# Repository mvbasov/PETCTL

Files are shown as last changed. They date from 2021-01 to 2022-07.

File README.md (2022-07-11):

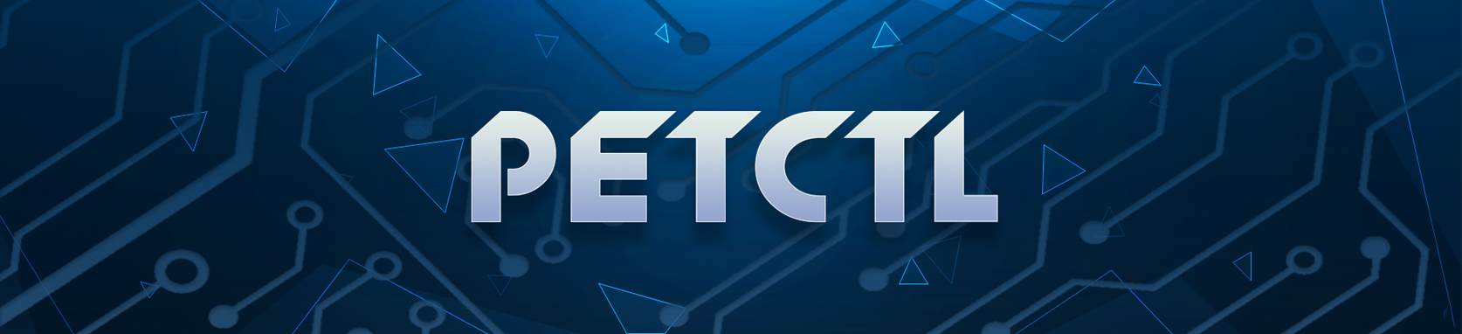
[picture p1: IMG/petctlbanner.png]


# PETCTL

Это контролер управляющий станком преобразующим ленту нарезанную из PET бутылок в волокно пригодное для 3D печати.

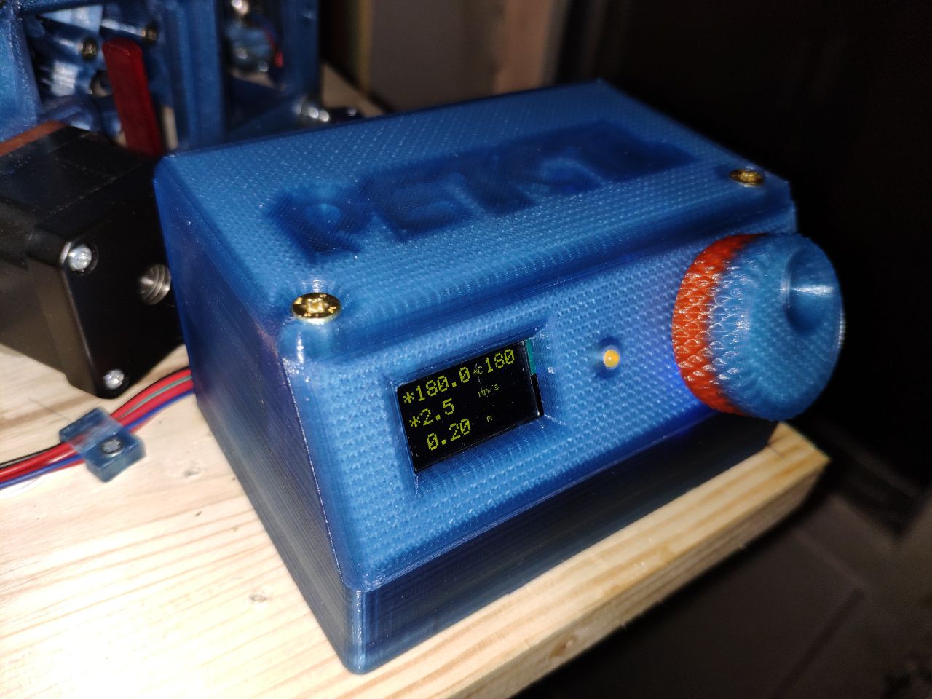
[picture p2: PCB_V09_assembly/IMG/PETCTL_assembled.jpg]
PETCTL assembled


Вот схема:

---

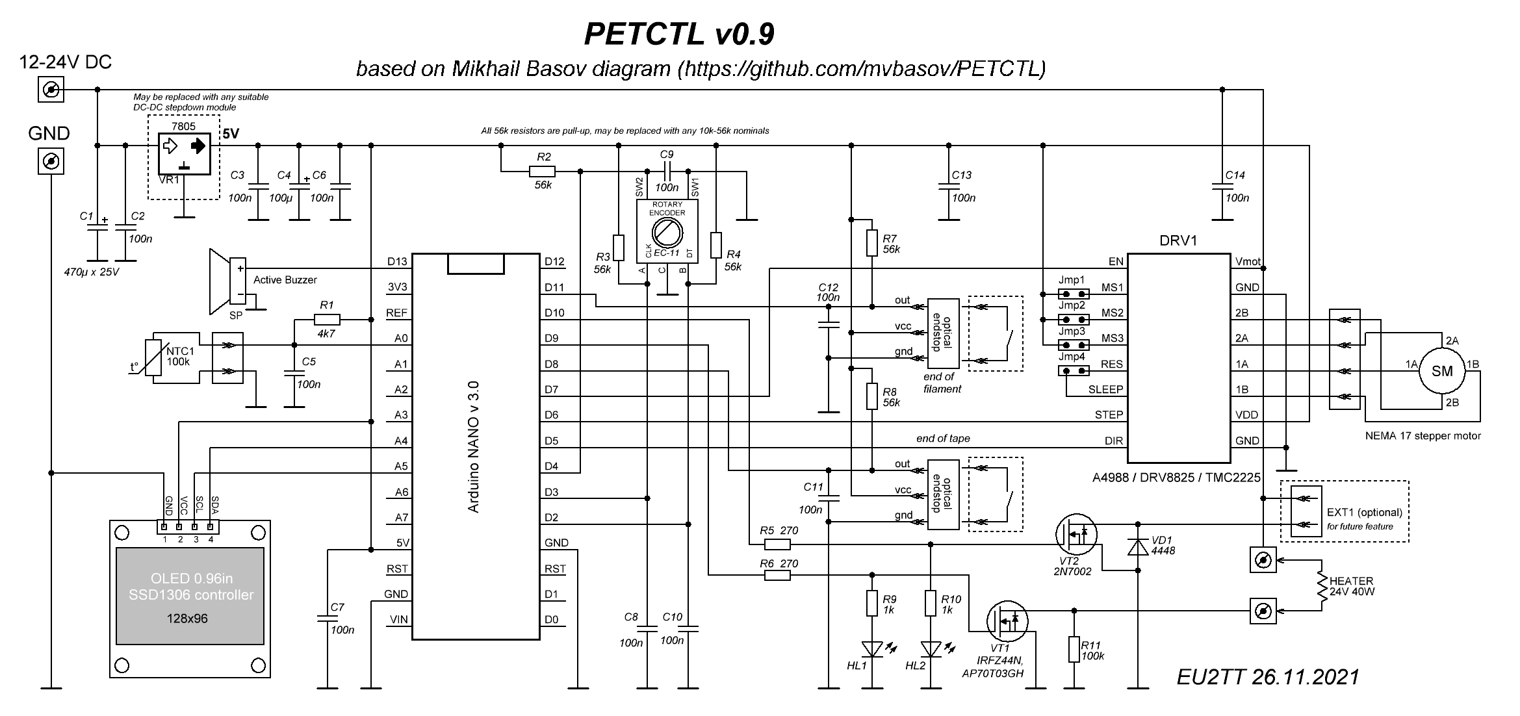
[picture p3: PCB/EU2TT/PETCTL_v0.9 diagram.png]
PETCTL scheme


**Спасибо** [EU2TT](https://github.com/EU2TT) за помощь в облагораживании и доработке схемы.

---

- В данный момент контроллер используется для управления [редуктором PETPull-2](https://drive.google.com/drive/mobile/folders/1PTYfURWS0YwCPlCB0__WyJwqnNEWJszi/1sBVlF62mEFIv8p1nZIAzGzY9kn1hc471/1dZt_md5HvzvhJHkd0jt-X09GqNWF04Xx/17iroY9sDo6CCnm7w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) ([PETPull-2 на Thingiverse](https://www.thingiverse.com/thing:4900782))
- Нагревательный блок со стандартными нагревателем от принтера 24V 40W. Термистор, так же, от принтера.
- Питается от внешнего БП 3D принтера на 24V. Потребление не превышает 60 W. 
- [Фюзер (сопло) моей конструкции](https://github.com/mvbasov/PETCTL/tree/github/3D_models/HeatedBlock)
- [Печатная плата от EU2TT](https://github.com/mvbasov/PETCTL/tree/github/PCB/EU2TT). Габариты 100 x 50 мм. SMD компоненты 0805. Если есть непреодолимое желание то можно натянуть 0603. Это бета версия платы не очень удобная для монтажа и впихивания в корпус. Также, не удалось скомпановать корпус так чтобы можно было подключать USB кабель не разбирая корпуса. Возможно, будет улучшенная версия. Плата проверена и функционально полностью работоспособна. Под эту плату разработан [корпус](PCB_V09_assembly/3D_models) и написана [инструкция по сборке](PCB_V09_assembly/README.md)
- [Список подходящих компонентов](BOM.md)
- У меня нет желания, возможности и способностей создавать полноценный, хорошо повторяемый проект и поддерживать его как это [сделал уважаемый Zneipas](https://3deshnik.ru/forum/viewtopic.php?f=37&t=986), за что ему большое спасибо! Но на любые вопросы готов ответить, если будет не лень.
- Начальная схема предложена ɢᴇᴏʀɢɪʏ(@nehilo011)  но от неё уже осталось далеко не всё. Собственно, схема родилась из примеров от библиотек.
- Прошивка (скетч) на 90% состоит из [библиотек AlexGyver отсюда](https://alexgyver.ru/lessons/gyverlibs/) и [отсюда](https://github.com/AlexGyver/GyverLibs).

# Как управлять
Управление получилось очень удобное (для меня):
- один клик регулировка температуры. Подсвечивается целевая температура справа в углу. В этом режиме длинное нажатие включает/выключает нагреватель, загорается/гаснет звёздочка в начале 1-й строки.
- два клика регулировка скорости. Подсвечивается скорость в середине. В этом режиме длинное нажатие включает/выключает двигатель, загорается/гаснет звёздочка в начале 2-й строки.
- Если ничего не нажимать 15 секунд переходит в ждущий режим как на фото.
- Если подключен датчик окончания ленты то после его срабатывания двигатель выключается после протяжки CFG_PULL_EXTRA_LENGTH [м] нагрев, тоже, выключается
- Если подключен датчик обрыва волокна то после его срабатывания двигатель выключается мгновенно и нагрев, тоже, выключается

# Общая компановка станка
Станок смонтирован на мебельном щите (хвойный) размером 43 x 29.5 см из рассчёта что его можно убрать в стандартный складной хозяйственный пластиковый ящик.

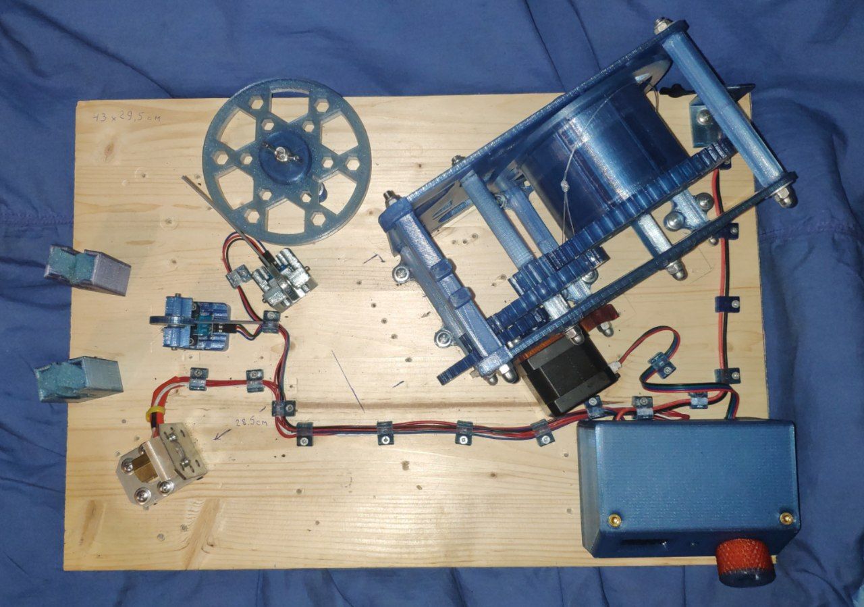
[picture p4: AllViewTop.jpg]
PETCTL top view


# Благодарности
* [nehilo](https://github.com/nehilo) За первоначальную идею, баннеры и логотип проекта.
* [EU2TT](https://github.com/EU2TT) За облагораживание схемы и разработку печатной платы.
* [tim](https://github.com/tim631) За помощь в обработке изображений
* [Vasily Afanasyev](https://github.com/h4lf) За разработку передней панели с защёлками

# вот так всё начиналось
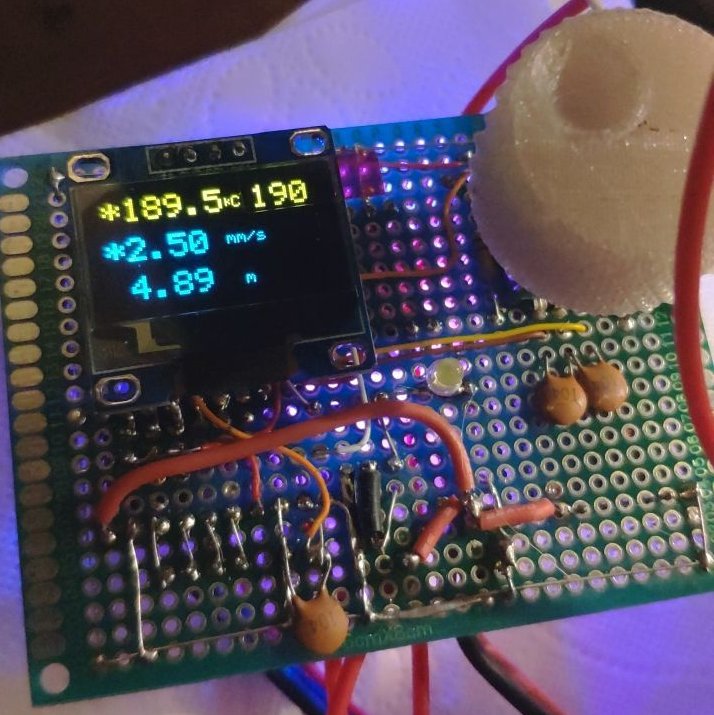
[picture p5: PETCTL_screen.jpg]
Screen photo


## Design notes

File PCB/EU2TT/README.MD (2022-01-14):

## Плата контроллера PETCTL v 0.9

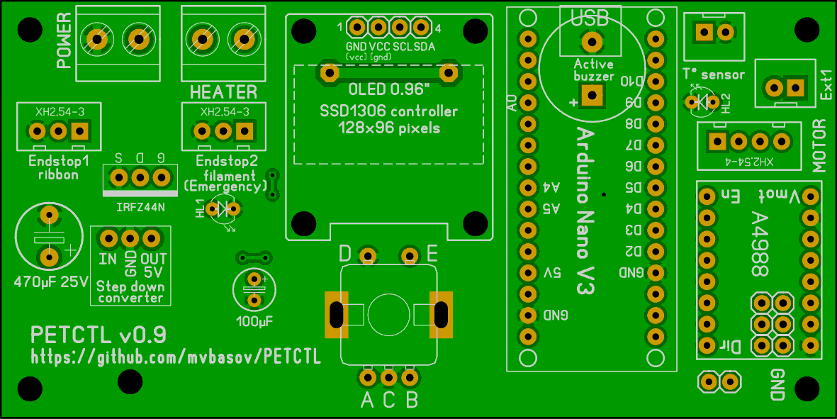
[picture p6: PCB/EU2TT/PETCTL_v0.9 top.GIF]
PETCTL v 0.9 top picture

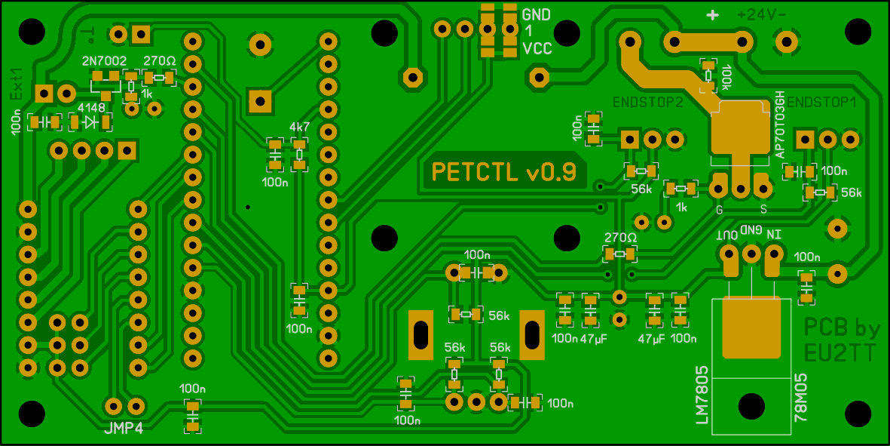
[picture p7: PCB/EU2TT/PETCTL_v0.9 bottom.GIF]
PETCTL v 0.9 bottom picture


Основная идея проекта - возможность его повторения всеми желающими. Печатную плату можно сделать используя ЛУТ, фоторезист или заказать на любом из сервисов по изготовлению печатных плат, к примеру JLCPCB. Архив с GERBER-файлами прилагается. А также оригинальный файл в Sprint Layout, "фотография" платы, рисунки шелкографии на верхней стороне платы, монтажная схема нижней стороны и PDF файл рисунка платы для изготовления по технологии ЛУТ и фоторезист. При печати для ЛУТ изображение НЕЛЬЗЯ масштабировать и зеркалить!

Отличия от предыдущих версий - уменьшено количество элементов, изменено расположение элементов, чтобы в двухстороннем варианте платы разъемы можно было монтировать как с верхней, так и с нижней стороны, добавлен второй концевик, сигнализирующий окончание прутка, 

В качестве стабилизатора может быть использовано то, что есть под рукой, SMD 78M05 либо LM7805 и аналоги, или любой подходящий импульсный понижающий преобразователь на 5 вольт, вариантов которого на Алиэкспресс развелось огромное количество.

Все пассивные SMD элементы типоразмера 0805.

Возможные варианты использования силового MOSFET в копусе TO-252 (установка с нижней стороны платы): https://alltransistors.com/ru/mosfet/crsearch.php?id=20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

Enlgish variant:
https://alltransistors.com/mosfet/crsearch.php?id=20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

Варианты использования силового MOSFET в копусе TO-220 (установка с верхней стороны платы): 
https://alltransistors.com/ru/mosfet/crsearch.php?id=20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

Enlgish variant:
https://alltransistors.com/mosfet/crsearch.php?id=20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

**В связи с тем, что у разных экземпляров OLED дисплеев полярность питания может отличаться, выбор нужного варианта питания осуществляется пайкой соответствующих перемычек, размещенных на плате.**

 Полярность подключения терморезистора и нагревательного элемента значения не имеет.
 При отсутствии электролитического конденсатора 100 мкФ, устанавливаемого на выходе стабилизатора питания можно установить два (или один) керамических в SMD 0805 емкостью 22-47 мкФ.
 Все подтягивающие резисторы 56к могут быть заменены на любые имеющиеся, в диапазоне 10к-56к.
 Оптические концевики использованы с низким уровнем срабатывания, для совместимости с механическими концевиками, выбирайте любой из имеющихся у вас. При использовании механических концевиков задействуются крайние контакты разъемов.
 При желании кнопку аварийной остановки можно подключить параллельно Endstop2 (filament) концевику.

### Назначение файлов:

* PETCTL v0.9 diagram.pdf 	- схема в формате PDF
* PETCTL v0.9 diagram.png		- схема в формате PNG
* PETCTL_v09_GERBERS.zip  	- архив с файлами для заказа на производстве
* PETCTL_v0.9 top.GIF			- внешний вид платы с верхней стороны
* PETCTL_v0.9 bottom.GIF		- внешний вид платы с нижней стороны
* PETCTL_v0.9 Top (Assembly Drawing).pdf		- монтажная схема верхней стороны
* PETCTL_v0.9 Bottom (Assembly Drawing).pdf	- монтажная схема нижней стороны
* PETCTL_v0.9_BC_LUT.pdf		- рисунок платы для изготовления методом ЛУТ. НЕ МАСШТАБИРОВАТЬ, НЕ ЗЕРКАЛИТЬ!

### Файлы, необходимые для изготовления платы методом негативного фоторезиста:

* PETCTL_v0.9_BC.pdf			- нижняя сторона, медь
* PETCTL_v0.9_BM.pdf			- нижняя сторона, паяльная маска
* PETCTL_v0.9_BS.pdf			- нижняя сторона, шелкография
* PETCTL_v0.9_TS.pdf			- верхняя сторона, шелкография

### Дополнительная инормация
В версии платы 0.8 для корректной работы энкодера в файле PETCTL_cfg.h следовало произвести нижеописанные изменения:
```
#define CFG_ENC_CLK 2
#define CFG_ENC_DT 3
```
В версии платы 0.9 этих изменений делать не нужно.

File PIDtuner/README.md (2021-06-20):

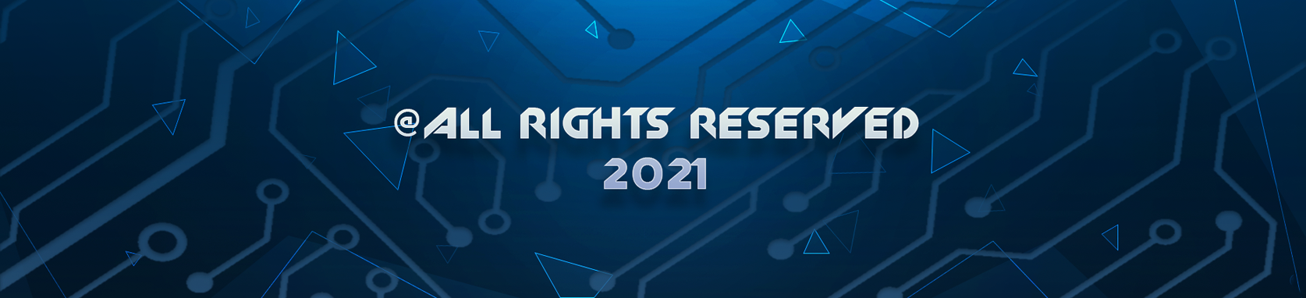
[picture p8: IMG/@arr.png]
top banner


# PID tuner

Подобрать коэффициенты PID регулятора нагревателя можно с помощью этого скетча.
Скетч загружается **вместо** основной прошивки. Время работы скетча не менне 20 минут. Результат работы отображается на экране и в serial console. Коеффициенты P, I и D нужно руками перенести в файл PETCTL_cfg.h

Example:
```
#define CFG_PID_P 12.69
#define CFG_PID_I 0.71
#define CFG_PID_D 57.11
```

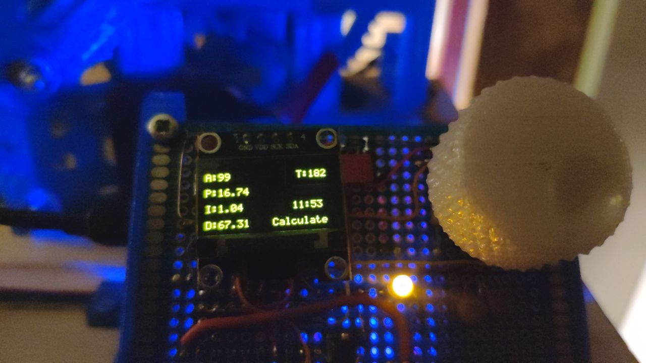
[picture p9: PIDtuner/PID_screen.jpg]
Screen photo


Тюнер совсем не идеальный. За несколько раз можно прткинуть какие коэффициенты должны быть. Мой  результат после тюнера: при разогреве "закидывает" на 10° в плюс, потом сбрасывает на 2° а потом держит стабильно. Для реальной работы приемлемо.

bottom banner

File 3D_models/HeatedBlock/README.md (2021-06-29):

## Описание кострукции фюзера

Фюзер состоит из нагревательного блока и сопла.

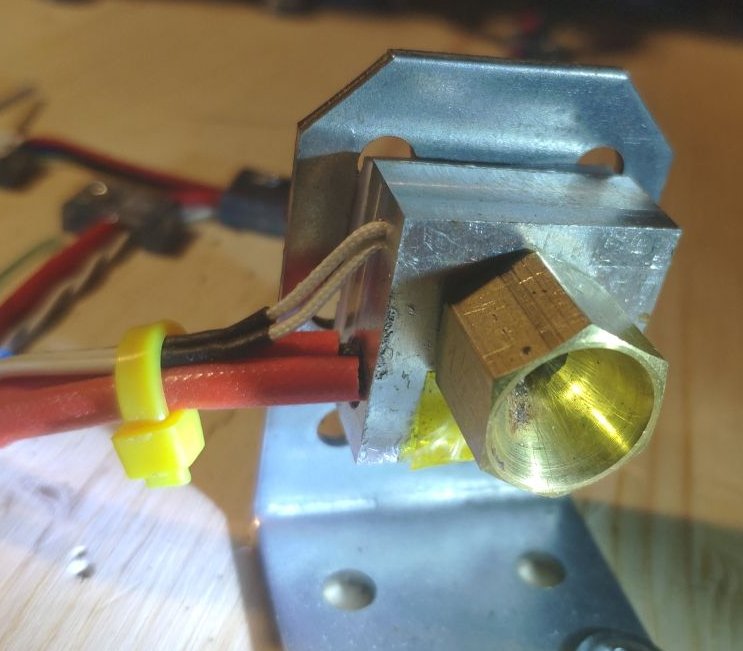
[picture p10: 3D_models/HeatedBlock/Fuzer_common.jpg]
Общий вид фюзера

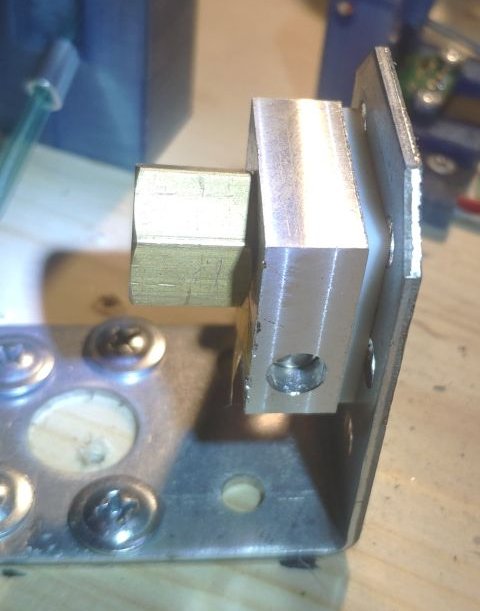
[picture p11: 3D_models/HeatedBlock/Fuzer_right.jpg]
Общий вид фюзера (спрва)

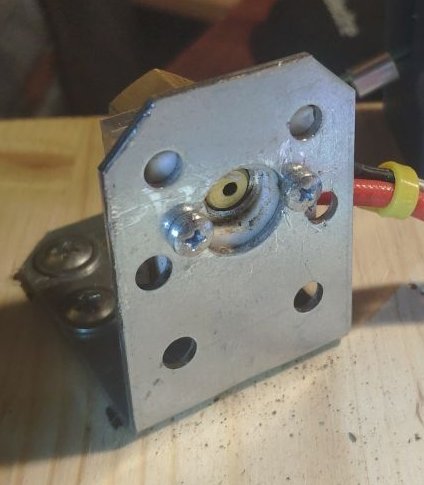
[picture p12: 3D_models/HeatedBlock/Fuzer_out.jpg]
Общий вид фюзера (выход)


#### Нагревательный блок

Нагревательный блок изготовлен из аллюмииниевого бруска размером 24 Х 24 Х 10 мм. Резьба под сопло M8. 
Канал под нагревательный элемент 6.1 мм сквозной. Используется стандартный нагревательный элемент от 3D принтера мощьностью 40 Вт на напряжение 24 В. 
Нагревательный эламент закреплён винтом M3. Канал под термистор 2 мм глубиной 5 мм. Нагревательный блок закреплён на стальном уголке двумя винтами М3.

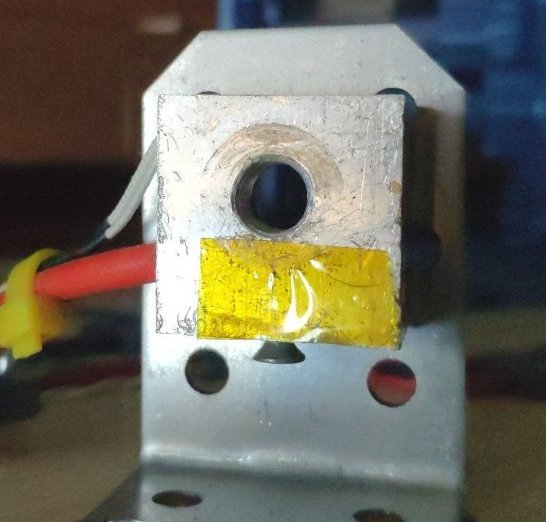
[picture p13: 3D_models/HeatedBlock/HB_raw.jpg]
Нагревательный блок

Чертёж для изготовления термоблока

#### Сопло

Сопло изготовлено из 6-и гранной латунной заготовки на токарном станке. Размер между гранями 14 мм длинна 22. 
Конус для подачи ленты сформирован коническим сверлом для кафеля оживальной формы номинальным разменом 12 мм. 
При формировании конуса в начале тонкого канала образуется небольшая "ступенька" которую нужно убрать в процессе полировки.

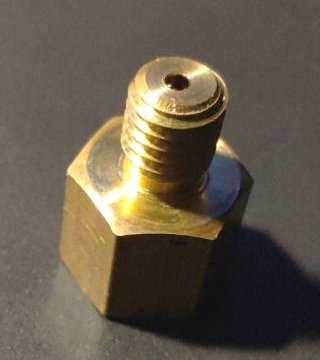
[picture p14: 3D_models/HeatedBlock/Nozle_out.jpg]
Сопло (выход)

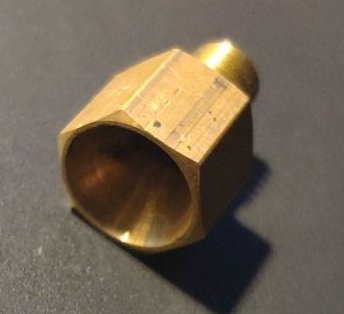
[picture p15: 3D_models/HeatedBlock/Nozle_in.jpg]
Сопло (вход)

Чертёж для изготовления сопла

#### Сверло
Хвостовик сверла обрезн до размера 75 мм для уменьшения вибрации при работе. Поверхность конуса отполирована. 

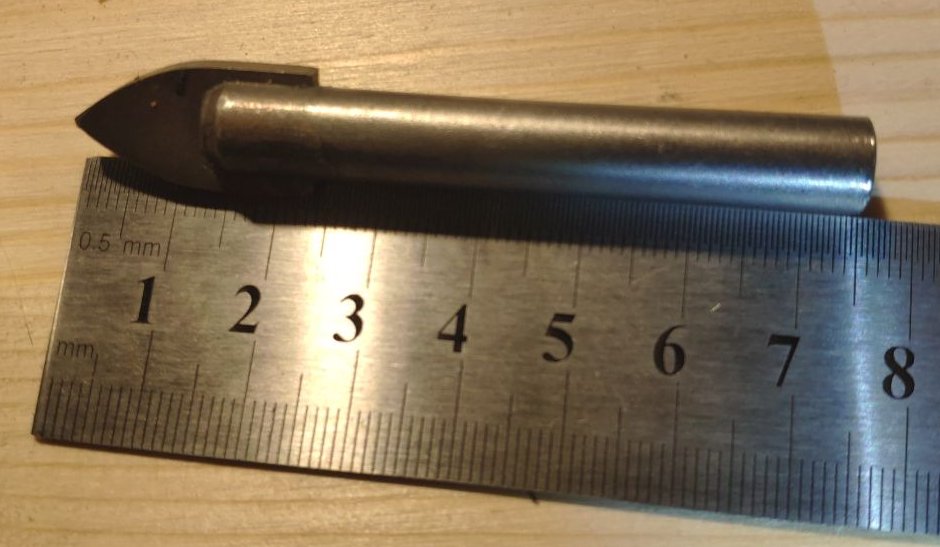
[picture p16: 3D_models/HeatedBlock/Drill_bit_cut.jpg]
Обрезнное сверло


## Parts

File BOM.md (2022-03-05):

### Список подходящийх компонентов

Ссылки могут быть афелированные. Участникам проекта на это пофиг. Если это вас не устраивает - не кликайте.

* *Arduino Nano*
  * [Iskra Nano Pro](https://amperka.ru/product/iskra-nano-pro) файлы конфигурации для Arduino IDE брать с сайта [Amperka.ru](http://wiki.amperka.ru/%D0%BF%D1%80%D0%BE%D0%B4%D1%83%D0%BA%D1%82%D1%8B:iskra-nano-pro)
  * [Arduino Nano v3 ](https://a.aliexpress.com/_99fklT) при прошивке указывать старый загрузчик.
  * [LGT8F328P LQFP32](https://a.aliexpress.com/_A61gLj) Уже не доступна к заказу. Использовал зелёную, без кварца. Код скорректирован для работы с этой платой.
* *Драйвер шагового двигателя*
  *  A4988, DRV8825 или ~~TMC2208~~(пока не у всех работает)
* *OLED дисплей* **(Внимание! выводы питания могут быть ровно наоборот!)**
  * [OLED](https://a.aliexpress.com/_AEG46X)
  * [OLED](https://a.aliexpress.com/_9g5hqT)
  * [OLED](https://www.aliexpress.com/item/32981934105.html) (информация [EU2TT](https://github.com/EU2TT))
  * [OLED](https://aliexpress.ru/item/32233342471.html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) (информация [nehilo](https://github.com/nehilo))
* *Энкодер*
  * [Энкодер 20 мм](https://a.aliexpress.com/_AW7f2p) использован при сборке PCB v0.9 TYPE2 в конфиге
  * [Энкодер 15 мм](https://a.aliexpress.com/_AX70XX)
  * [Энкодер](https://a.aliexpress.com/_9uJ3AL) Должен подойти
  * [Энкодер](https://aliexpress.ru/item/33038646005.html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) (информация [nehilo](https://github.com/nehilo))
* *Оптические датчики* При срабатывании должен давать 0 
  * [на транхзисторах](https://a.aliexpress.com/_9jbDPR)
  * [~~на компараторе~~](https://www.aliexpress.com/item/4000005190162.html) (информация [EU2TT](https://github.com/EU2TT))**Не подходит. Инверсный выход.**
* *MOSFET*
  * [IRFZ44N](https://aliexpress.ru/item/32844109027.html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) (информация [nehilo](https://github.com/nehilo))
  * [IRFZ44N](https://a.aliexpress.com/_Ao9Dql)
* *Понижающий преобразователь* можно использовать и LM7805
  * [5.5-32V to 5V 1A](https://a.aliexpress.com/_9Qambn)
* *Термистор, нагреватель*
  * [Термистор](https://a.aliexpress.com/_AA36o9)
  * [Нагреватель](https://a.aliexpress.com/_AsGAb7)

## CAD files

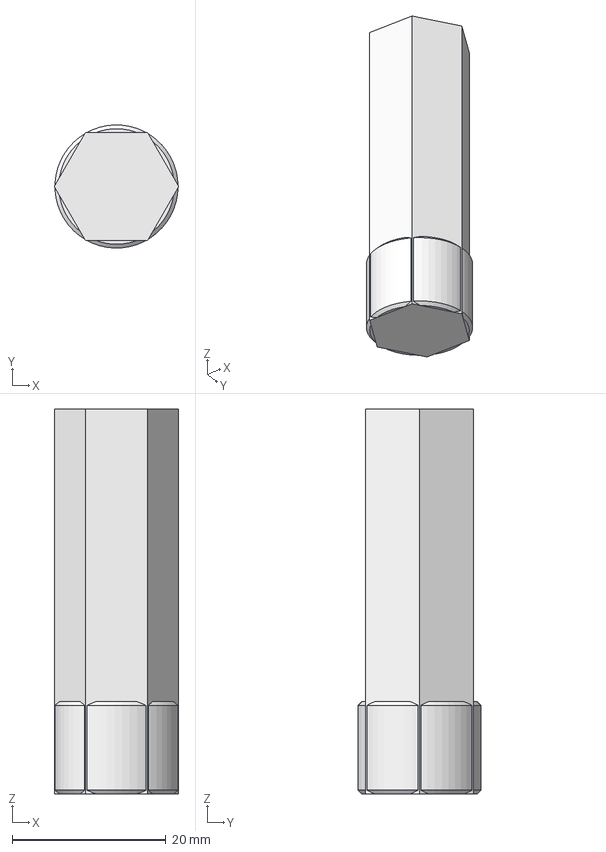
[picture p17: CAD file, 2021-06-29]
3D_models/HeatedBlock/FilPullNozzle_v2a.FCStd
16.2 x 16.0 x 50.0 mm

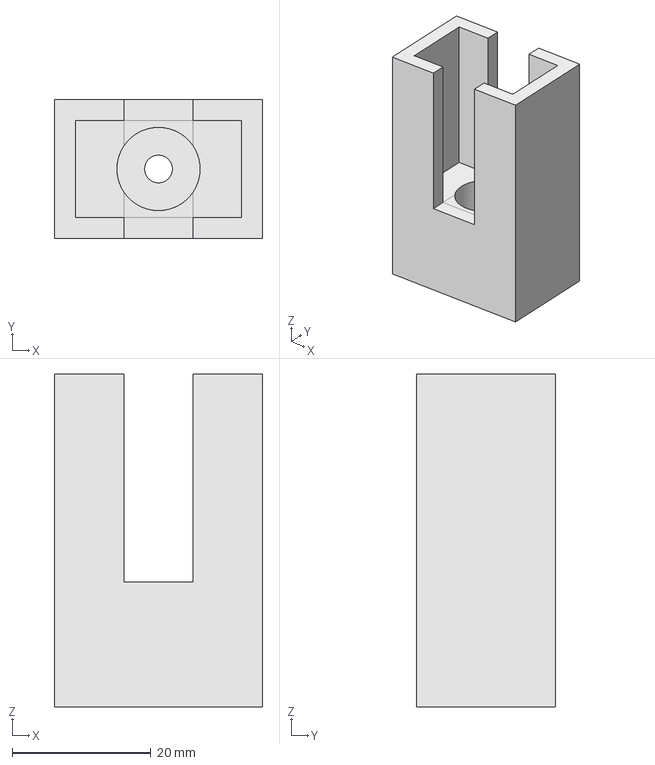
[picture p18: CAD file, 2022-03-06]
3D_models/StripeCleaner(asZenipas).FCStd
30.0 x 20.0 x 48.0 mm

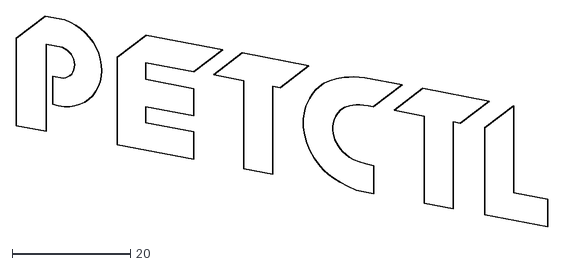
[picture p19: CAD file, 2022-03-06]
IMG/PETCTL_logo.dxf
89.8 x 35.6

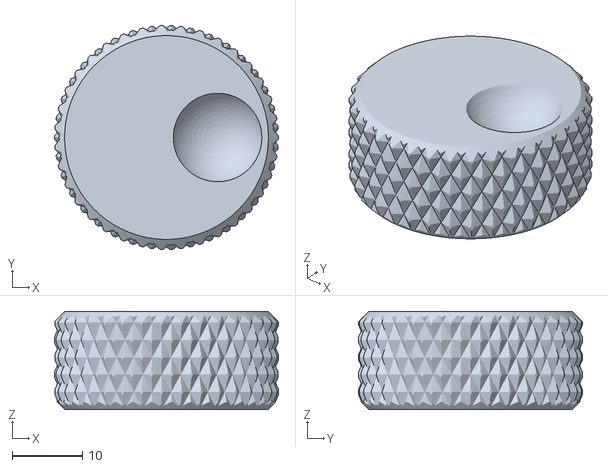
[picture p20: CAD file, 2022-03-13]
PCB_V09_assembly/3D_models/EncoderKnob-15mm-V3.stl
32.0 x 32.0 x 14.0

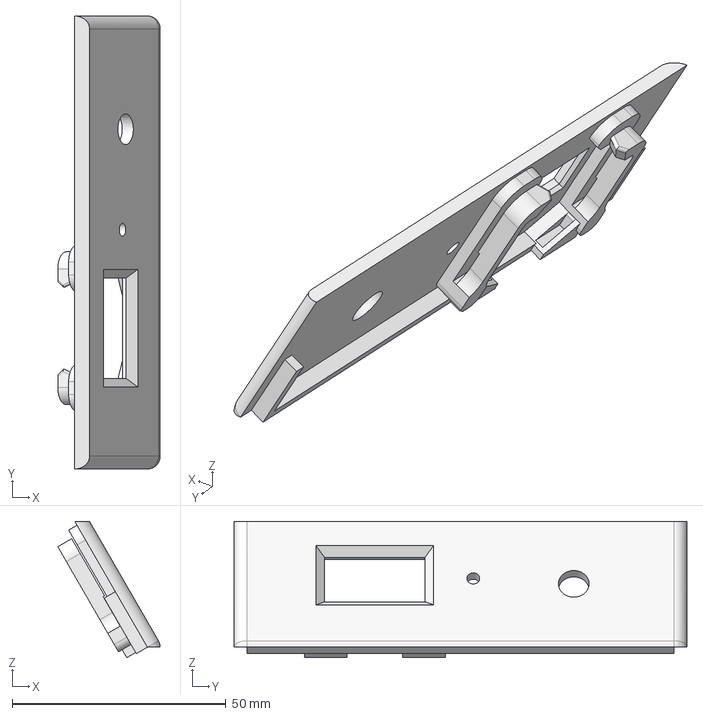
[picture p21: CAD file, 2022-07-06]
PCB_V09_assembly/3D_models/PETCTL_09PCB_case_V7-Front-ModLatch/PETCTL_CaseFrontLatch.step
24.0 x 106.0 x 31.9 mm

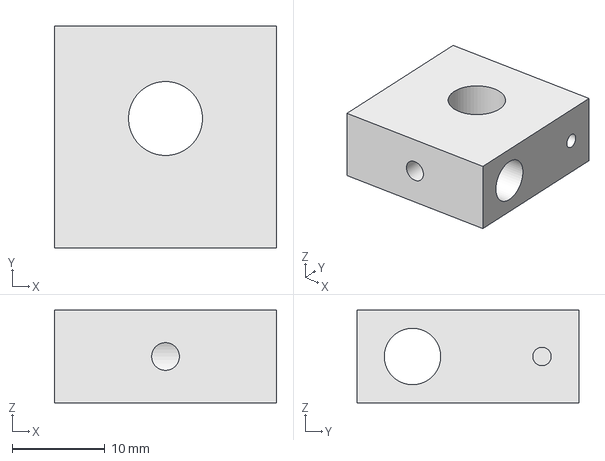
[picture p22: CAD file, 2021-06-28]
3D_models/HeatedBlock/FilPullHB_v1c.FCStd
24.0 x 24.0 x 10.0 mm

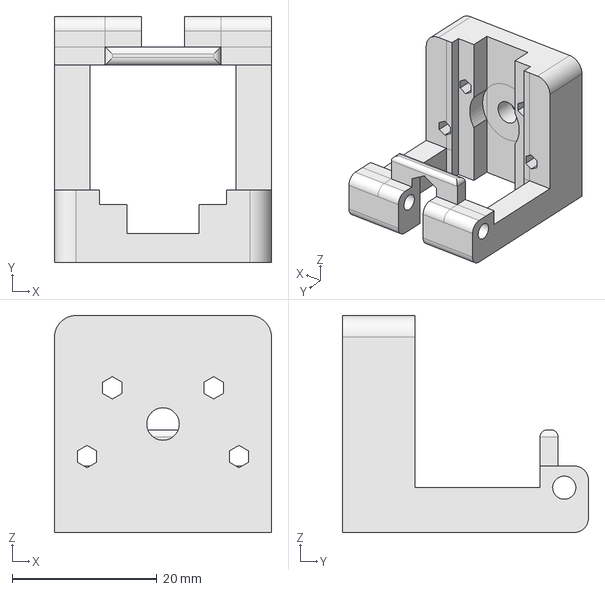
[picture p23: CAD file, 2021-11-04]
3D_models/OptoEndStopCase_v5.step
30.0 x 34.0 x 30.0 mm

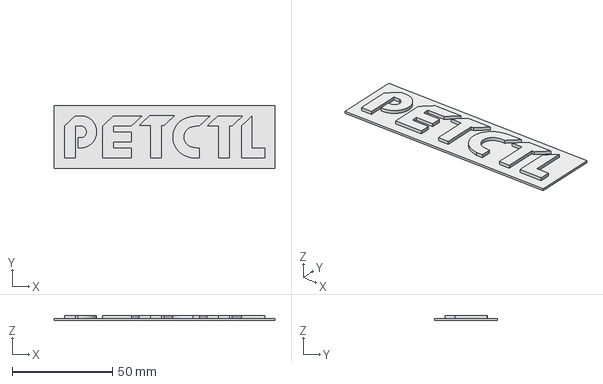
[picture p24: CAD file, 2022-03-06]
IMG/PETCTL_logo_V1.FCStd
110.0 x 31.1 x 2.50 mm

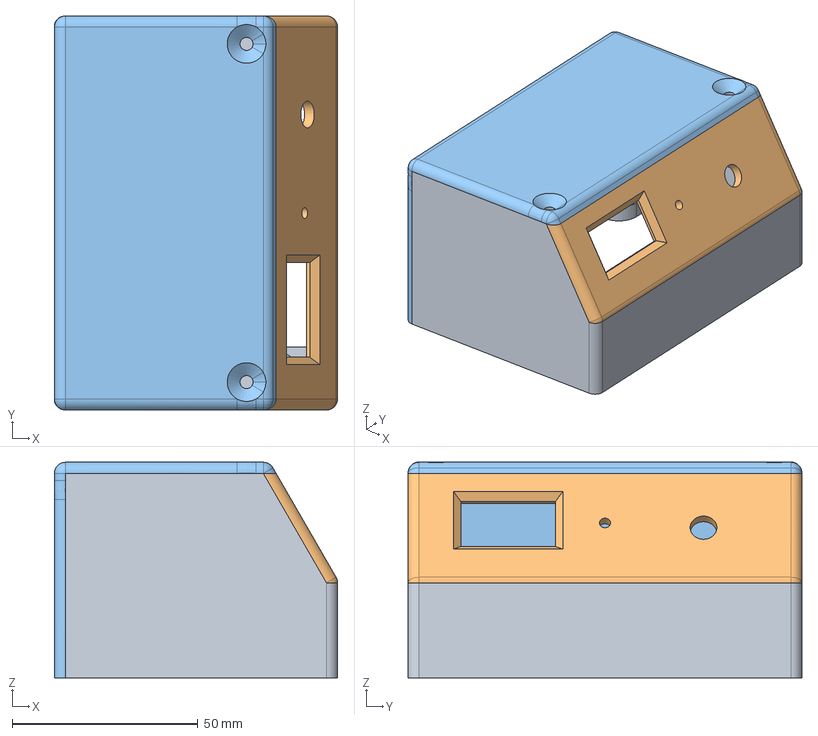
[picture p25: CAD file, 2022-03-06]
PCB_V09_assembly/3D_models/PETCTL_09PCB_case_V7.step
76.2 x 106.0 x 58.0 mm

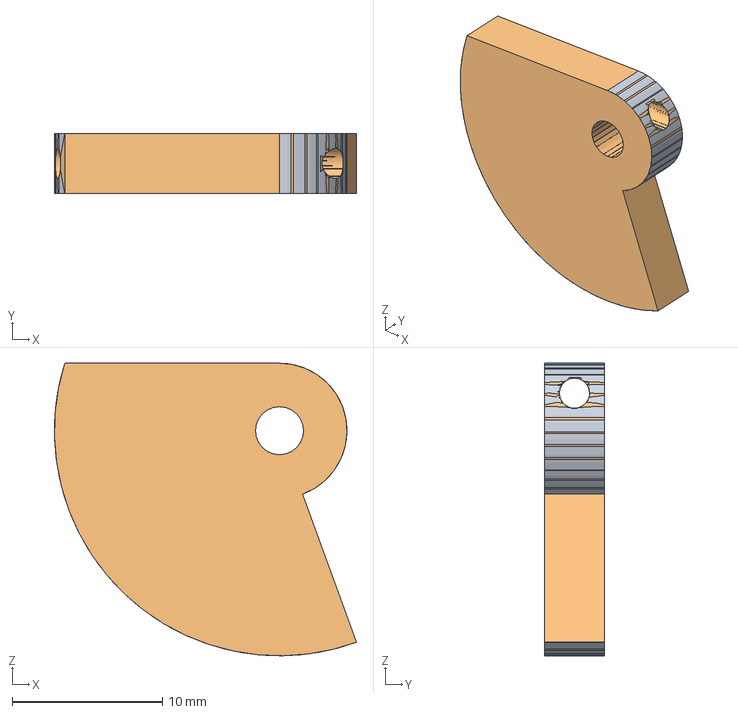
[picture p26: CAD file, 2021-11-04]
3D_models/OptoEndStopFlag_v3.FCStd
20.1 x 4.00 x 19.5 mm
bFlag
Pocket (Meshed)

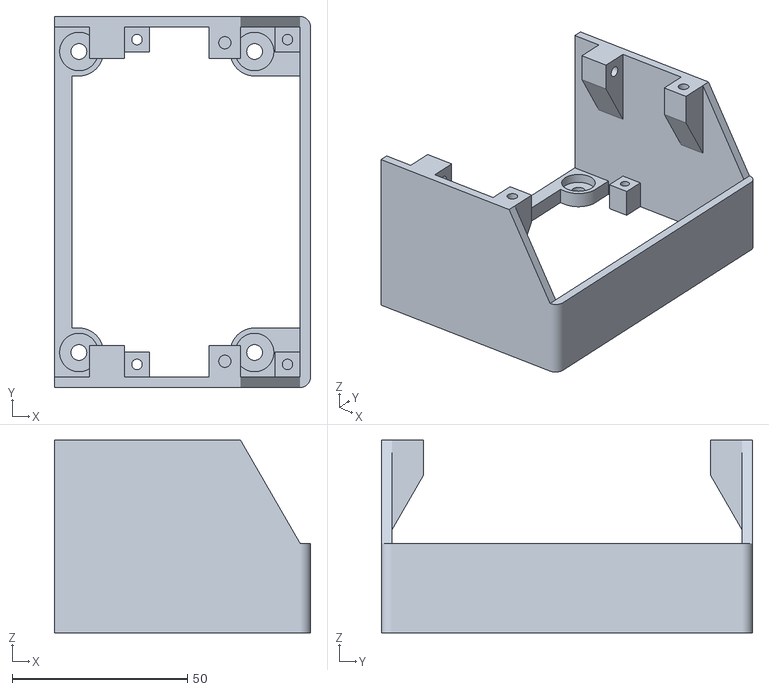
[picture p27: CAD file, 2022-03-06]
PCB_V09_assembly/3D_models/PETCTL_09PCB_case_V7-Base.stl
73.2 x 106.0 x 55.0

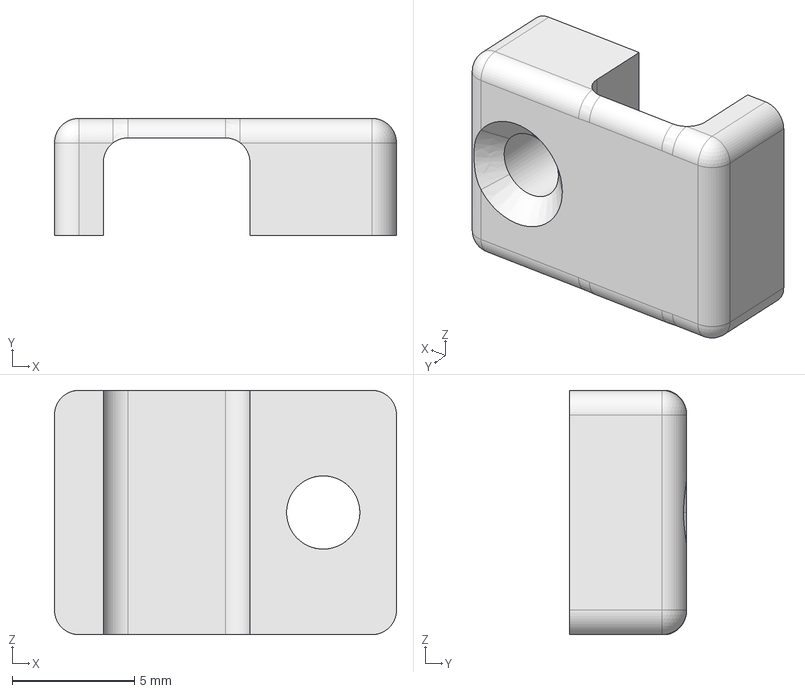
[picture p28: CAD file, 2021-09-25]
3D_models/CableClip_V1.step
14.0 x 4.80 x 10.0 mm

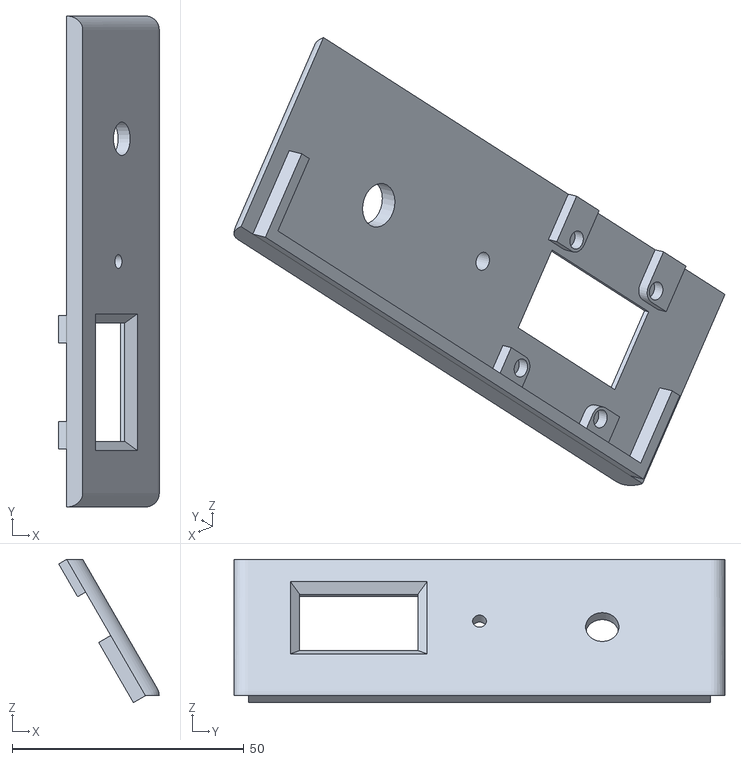
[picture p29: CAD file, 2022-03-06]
PCB_V09_assembly/3D_models/PETCTL_09PCB_case_V7-Front.stl
21.7 x 106.0 x 30.9

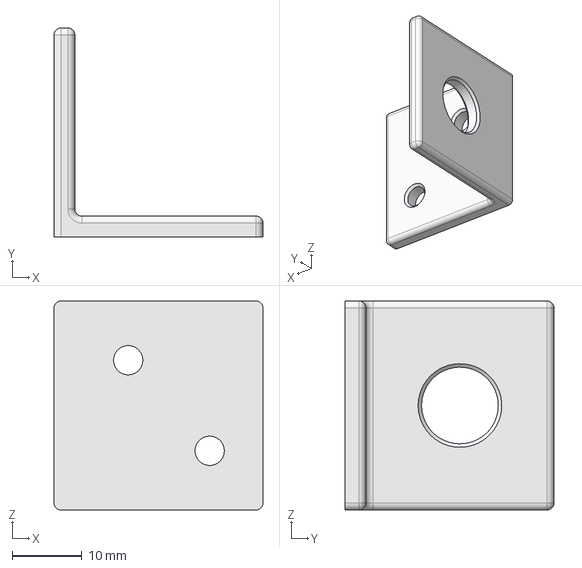
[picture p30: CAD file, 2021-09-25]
3D_models/PowerMount_V1.step
30.0 x 30.0 x 30.0 mm

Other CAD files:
PCB_V09_assembly/3D_models/PETCTL_09PCB_case_V7-TopBack.stl
PCB_V09_assembly/3D_models/EncoderKnob-20mm-V2.stl
3D_models/CableClip_V1.FCStd
3D_models/CableClip_V1.stl
3D_models/OptoEndStopCase_v5.FCStd
3D_models/OptoEndStopCase_v5.stl
3D_models/OptoEndStopFlag_v3.stl
3D_models/PowerMount_V1.FCStd
3D_models/PowerMount_V1.stl
3D_models/StripeCleaner(asZenipas).stl
PCB_V09_assembly/3D_models/PETCTL_09PCB_case_V7-Front-ModLatch/PETCTL_CaseFrontLatch.stl
PCB_V09_assembly/3D_models/PETCTL_09PCB_case_V7.FCStd

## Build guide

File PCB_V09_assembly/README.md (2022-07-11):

# Сборка платы v0.9 от EU2TT и монтаж её в корпус
## О версии платы
Это бета версия платы не очень удобная для монтажа и впихивания в корпус. Также, не удалось скомпановать корпус так чтобы можно было подключать USB кабель не разбирая корпуса. Возможно, будет улучшенная версия. Плата проверена и функционально полностью работоспособна. 

## Сборка платы
Файлы для изготовления платы и их описание можно найти [здесь](../PCB/EU2TT/README.MD).

Для монтажа платы используются резисторы и конденсаторы 100n типоразмера 0805 но, при большом желании, можно использовать типоразмер 0603:

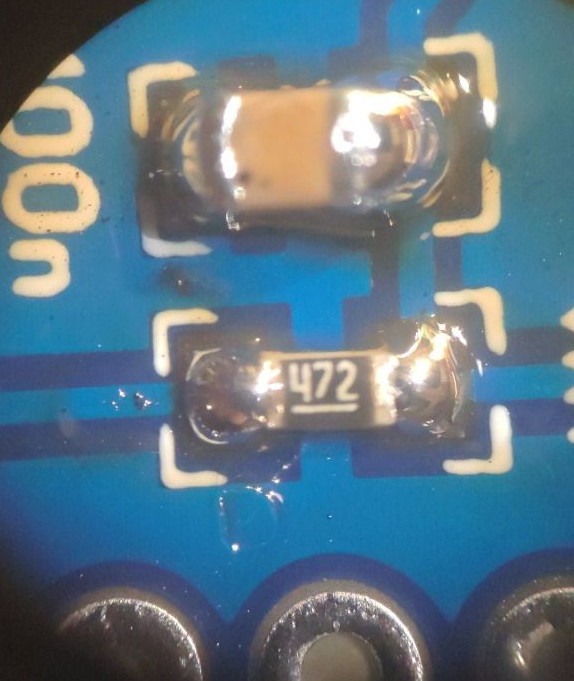
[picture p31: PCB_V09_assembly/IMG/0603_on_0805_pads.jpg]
0603 on 0805 pads


**Внимательно порочитайте** [описание платы](../PCB/EU2TT/README.MD) **особенно в части питания OLED**. Перемычки должны быть запаяны, например, так:

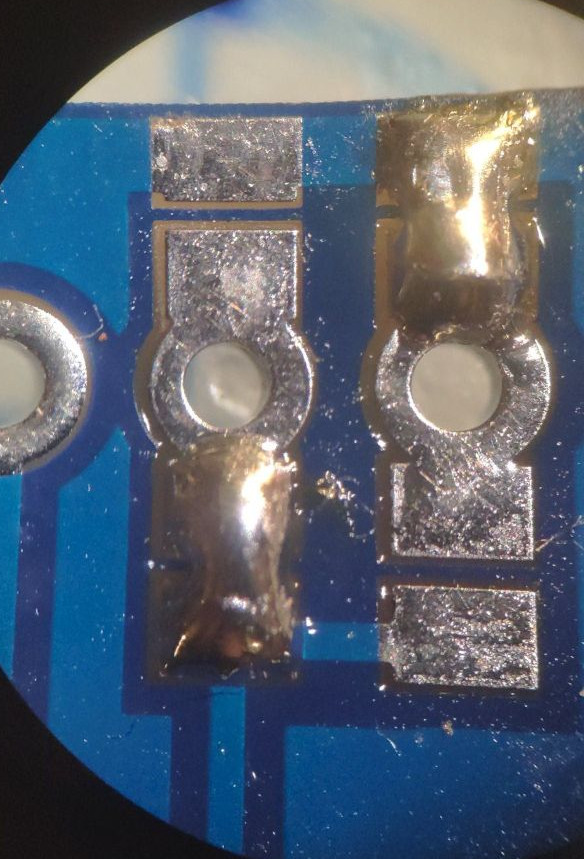
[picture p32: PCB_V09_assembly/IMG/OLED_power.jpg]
OLED power


Собранная плата выглядит так:

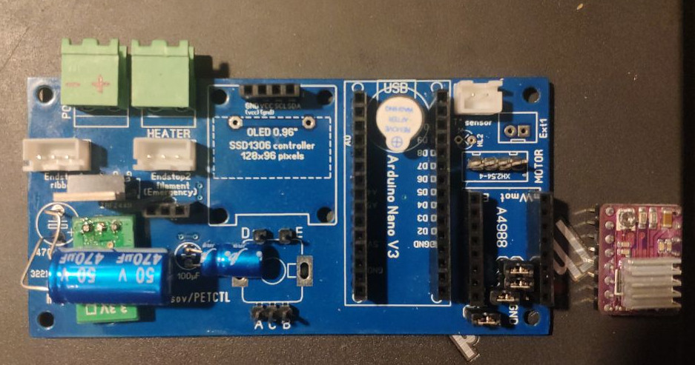
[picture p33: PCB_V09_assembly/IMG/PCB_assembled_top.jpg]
mounted_top

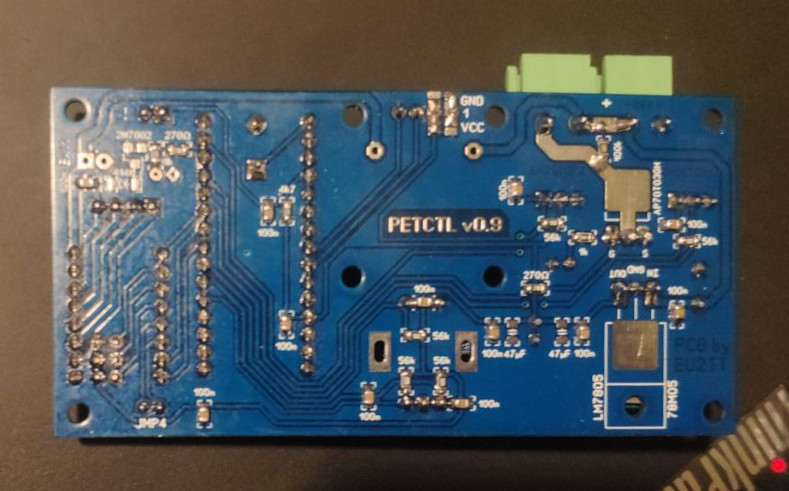
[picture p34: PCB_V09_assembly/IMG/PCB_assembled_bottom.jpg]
mounted_botom


Это первая, разработанная нами, версия (бета) платы и она не "оптимизированна" для сборки. Узел где расположен входной фильтрующий (конденсатор), преобразователь 24В в 5В и ключ нагревателя удалось собрать так:

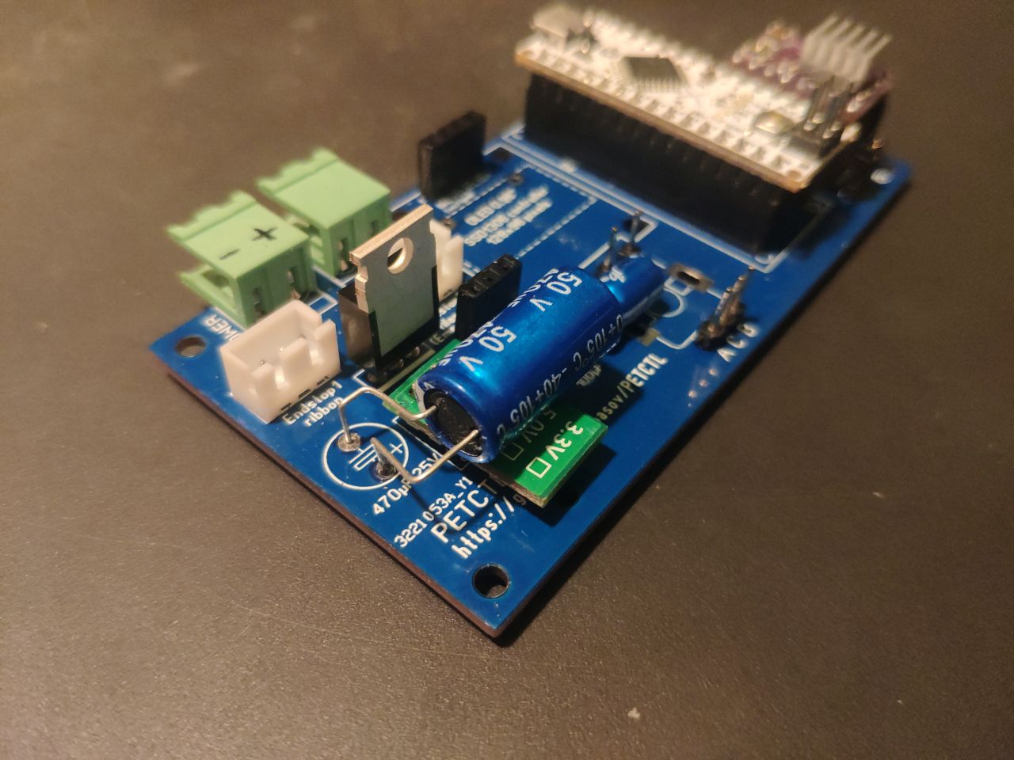
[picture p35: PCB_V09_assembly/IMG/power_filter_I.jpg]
power filter I

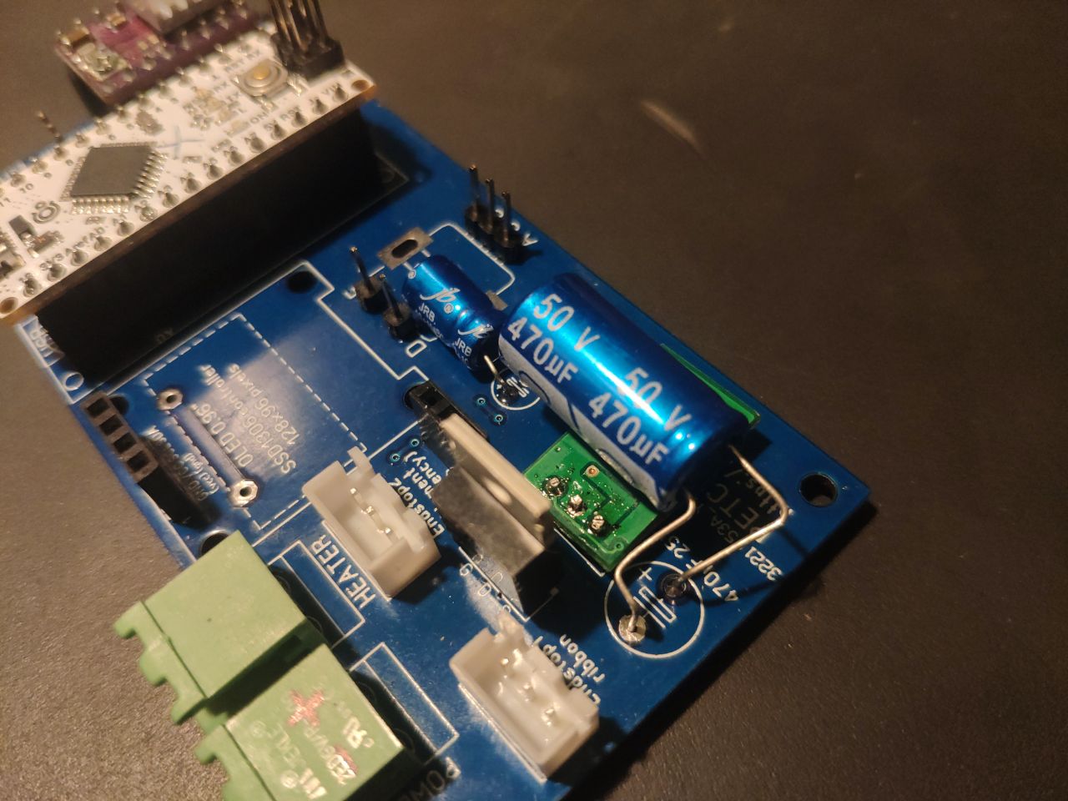
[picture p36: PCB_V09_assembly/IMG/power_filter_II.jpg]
power filter II

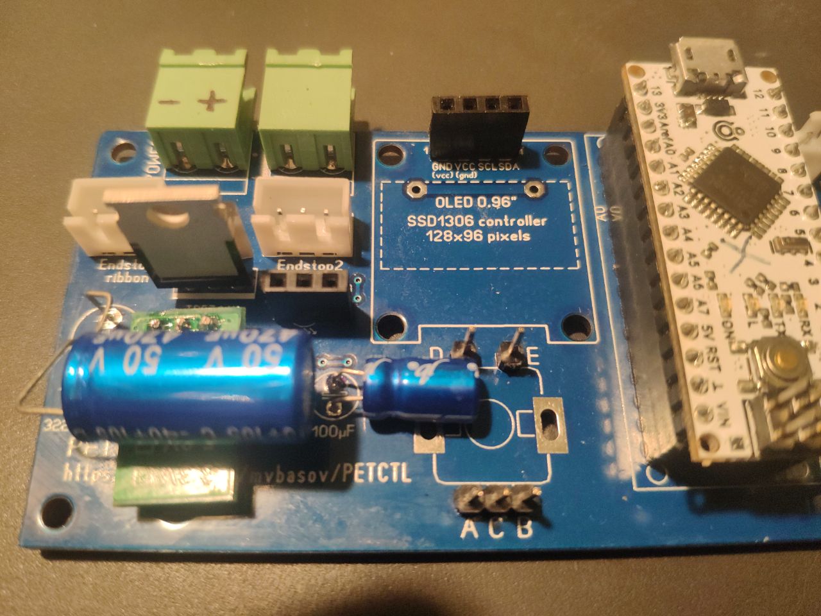
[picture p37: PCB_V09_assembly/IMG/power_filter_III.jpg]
power filter III


Обвязка дополнительного ключа (VT2, 2N7002) запаяны а сам ключ и светодиод нет. В прошивке это не используется. Резерв на будующее.

На плате Arduino nano разъема прямого программирования (ISP) быть не должно (на части фотографий он есть) - при сборке упрётся в выводы энкодера.

На место где на плате должен быть светодиод распаян 3-х контактный разъём с одним удалённым контактом (на фото правый). На кабеле идущем от светодиода с передней панели разъём, тоже, 3-х контактный и один контакт никуда не подключен. Это своеобразный аналог ключа на разъёме предотвращающий переполюсовку светодиода при не правильном включении.

Под эту плату был разработан корпус для монтажа на основание (деревянное) станка. Файлы для печати корпуса можно найти [здесь](3D_models/)

## Порядок сборки корпуса c платой и подключения кабелей
1. закрепляем основную часть корпуса на основании станка с помощью саморезов DIN968 4.2 x 16
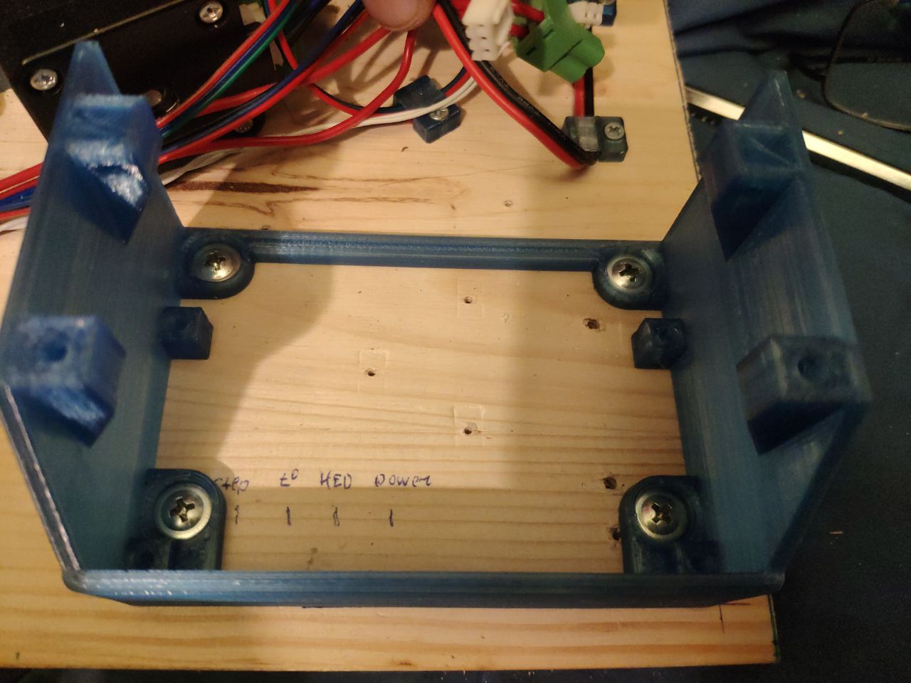
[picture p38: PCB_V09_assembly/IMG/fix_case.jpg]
fix case

2. закрепляем плату в основной части корпуса винтами DIN912 M3 x 5
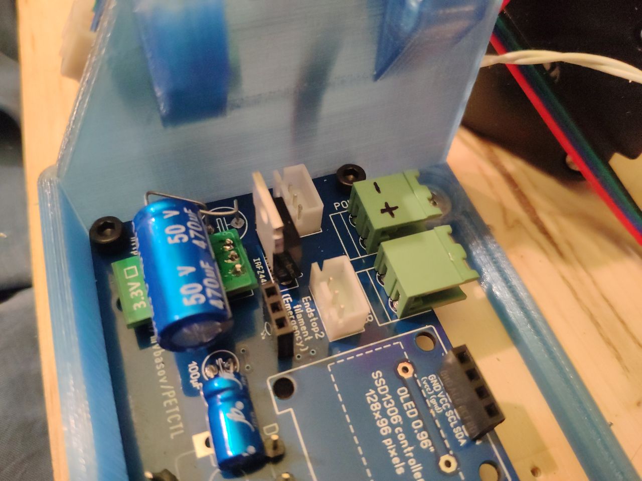
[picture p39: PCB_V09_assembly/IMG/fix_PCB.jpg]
fix PCB

3. подключаем кабели идущиё из корпуса наружу (питание, нагреватель, термистор, датчик окончания ленты, датчик обрыва прутка)
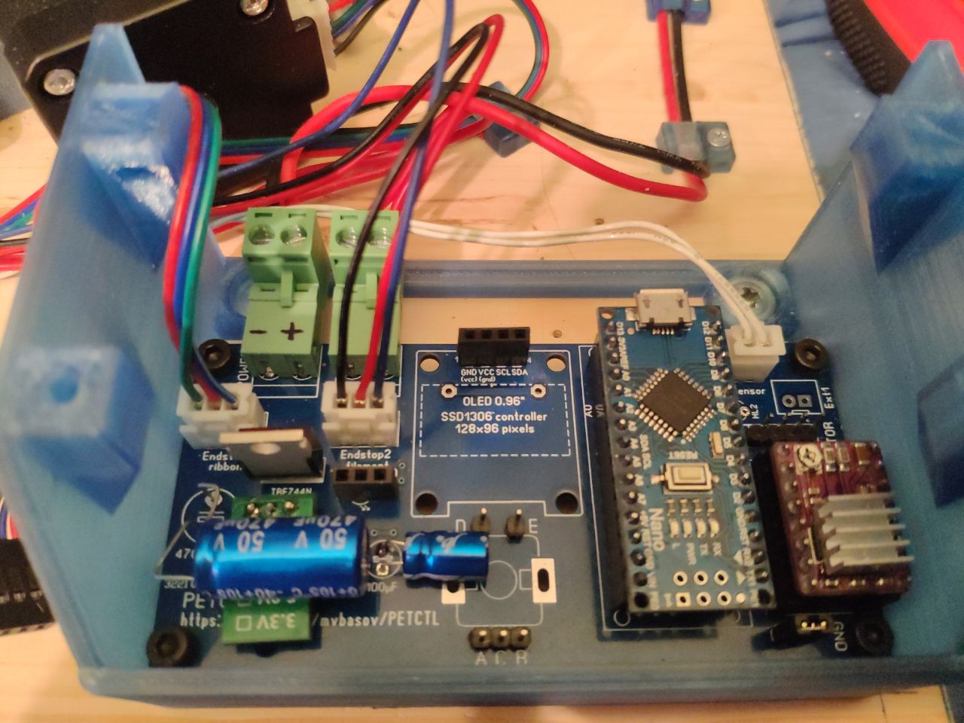
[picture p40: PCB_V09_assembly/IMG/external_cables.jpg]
external cables

4. монтируем на переднюю панель OLED, энкодер и светодиод и припаиваем кабели к энкодеру и светодиоду. Для OLED готовим кабель с разъёмами Dupont на конце. [Vasily Afanasyev](https://github.com/h4lf) разработал [переднюю панель](https://github.com/mvbasov/PETCTL/tree/github/PCB_V09_assembly/3D_models/PETCTL_09PCB_case_V7-Front-ModLatch) с крепление дисплея на защёлках.
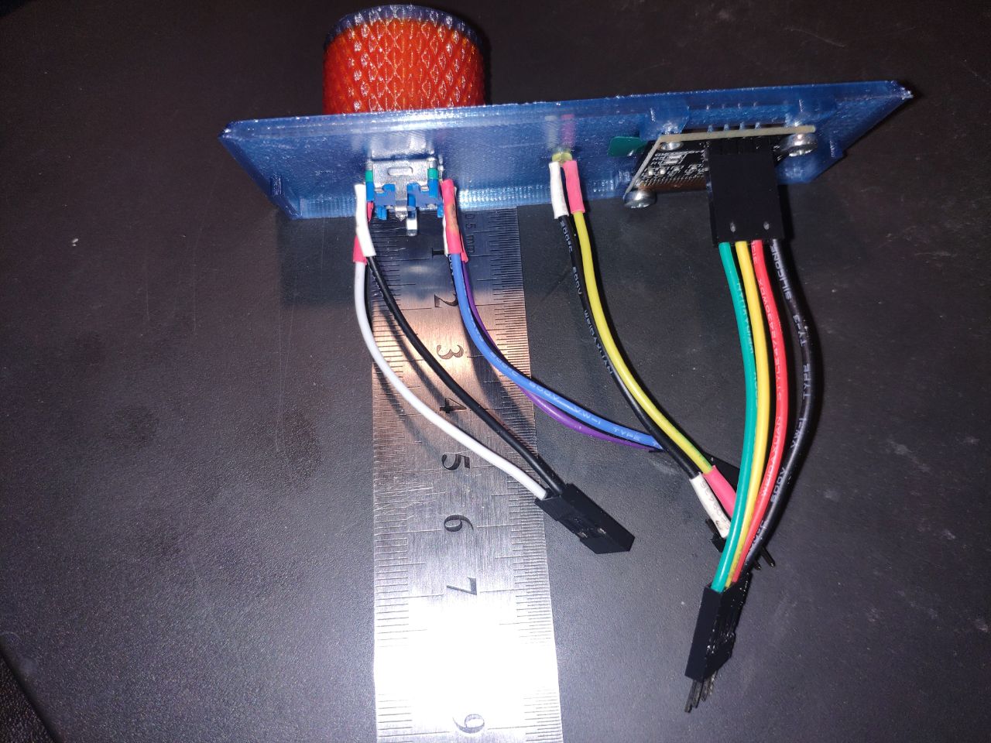
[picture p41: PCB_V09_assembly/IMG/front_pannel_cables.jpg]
front pannel cables

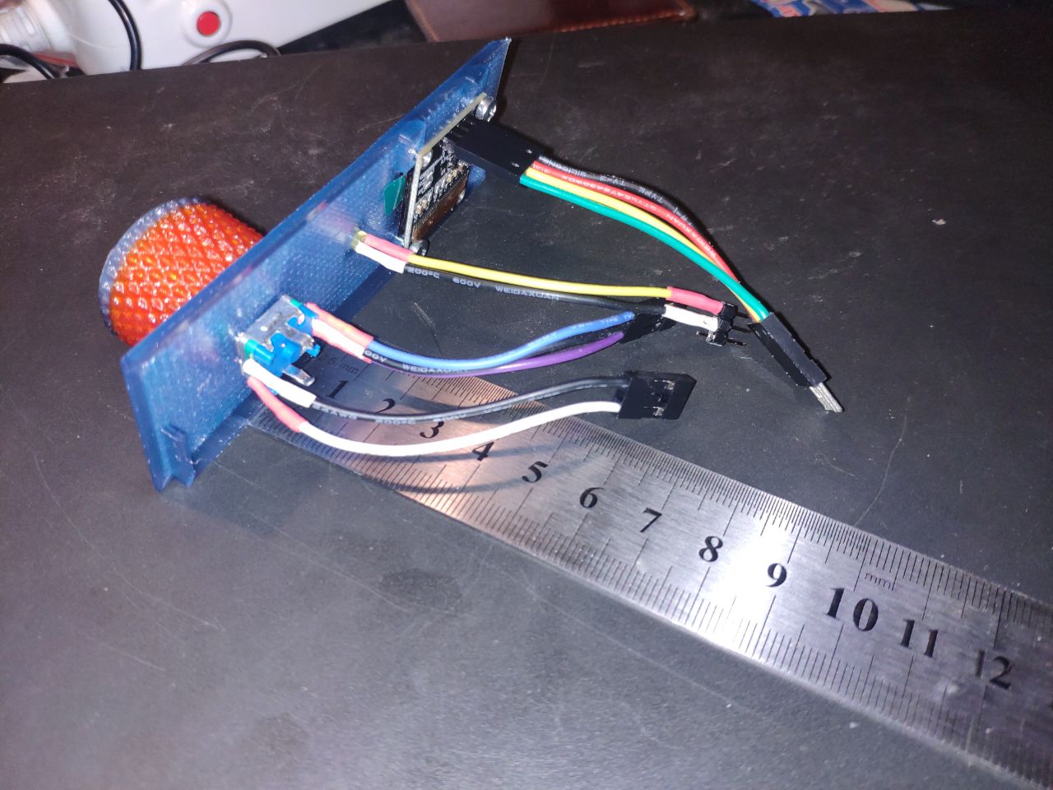
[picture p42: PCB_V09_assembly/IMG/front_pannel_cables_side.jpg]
front pannel cables side

5. устанавливаем переднюю панель на место, подключаем кабели к плате и фиксируем верхней/задней частью корпуса
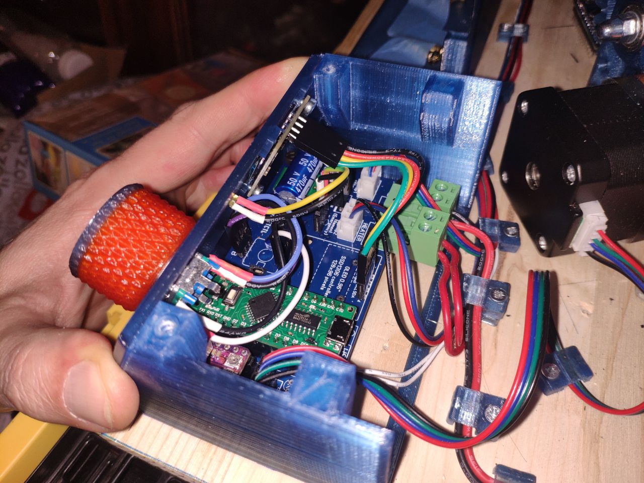
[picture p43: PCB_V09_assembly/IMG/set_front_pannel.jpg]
set front pannel

6. Прикручиваем верхнюю/заднюю часть корпуса саморезами DIN7982TX сверху 3.5 x 16, сзади 3.5 x 25
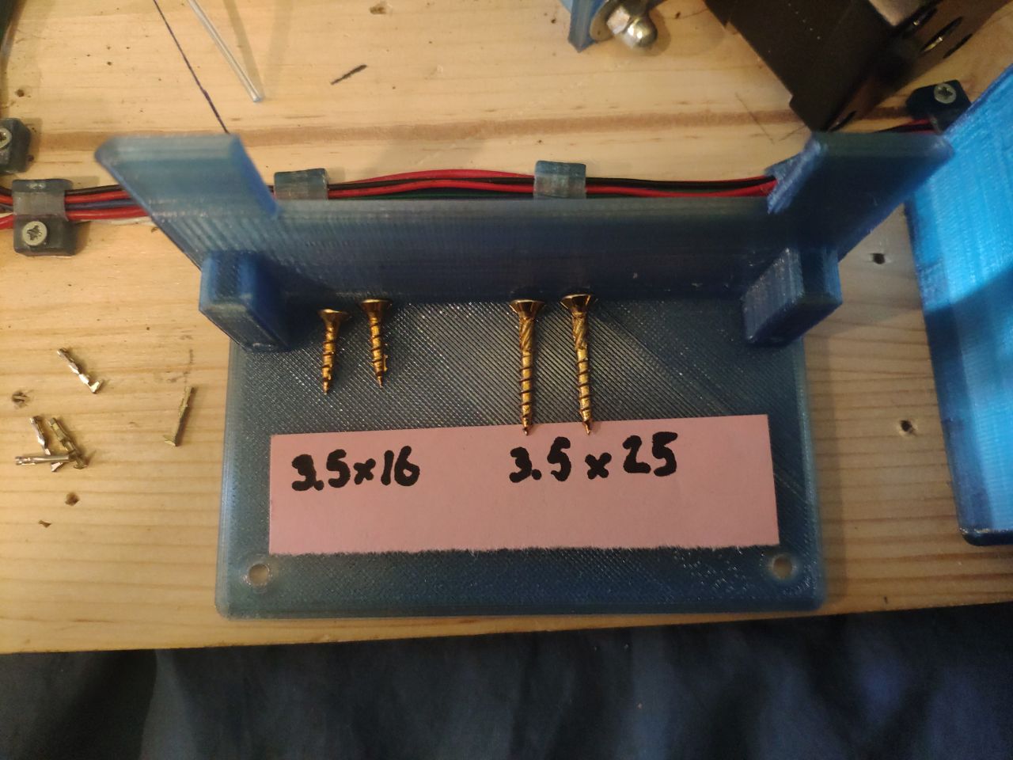
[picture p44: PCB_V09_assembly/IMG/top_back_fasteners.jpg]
top back fasteners

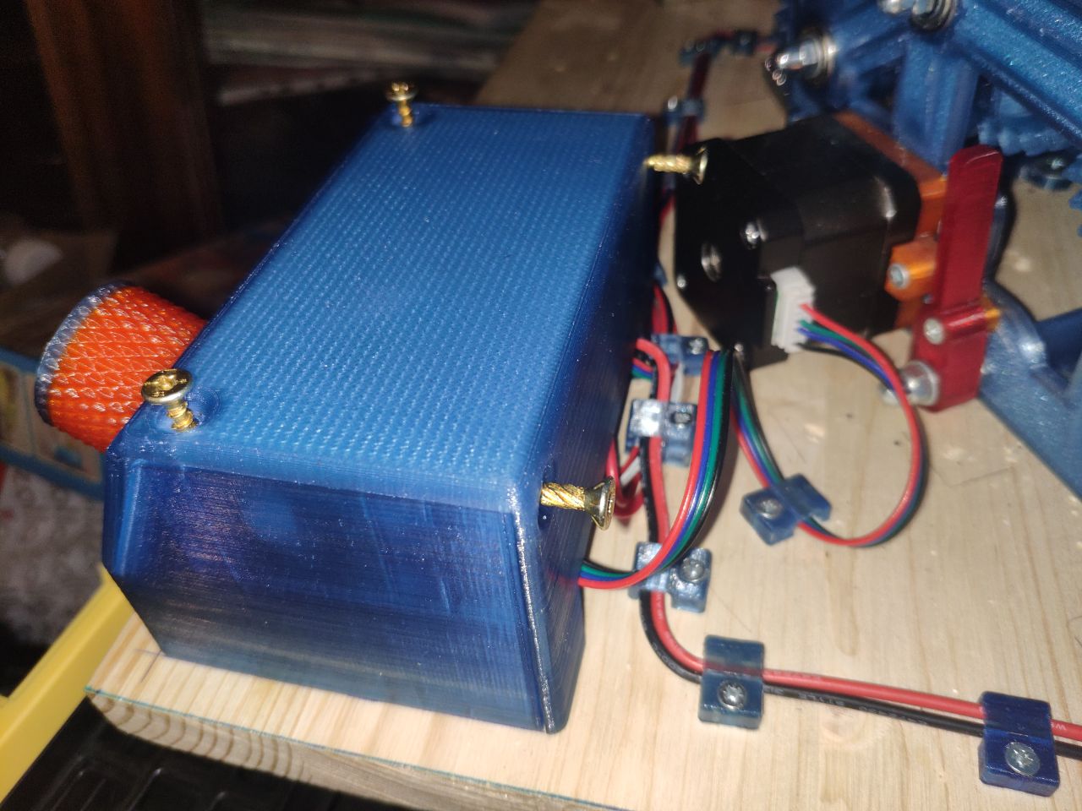
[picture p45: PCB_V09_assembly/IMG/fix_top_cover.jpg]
fix top cover

7. Наслаждаемся результатом :)
PETCTL assembled

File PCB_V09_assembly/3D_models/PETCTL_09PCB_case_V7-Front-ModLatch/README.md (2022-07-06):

## Вариант передней панели с креплением экрана на защёлках

Для установки необходимо немного отогнуть разём, который обведён красным на фотографии.

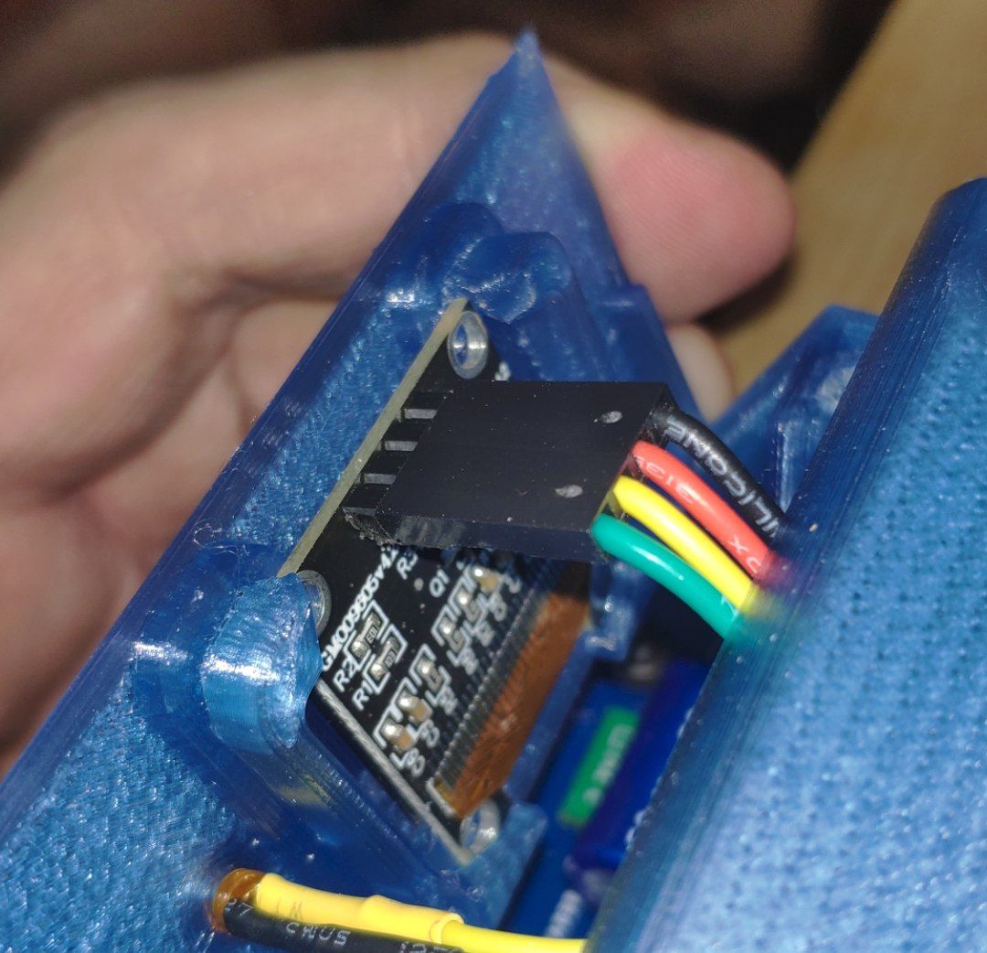
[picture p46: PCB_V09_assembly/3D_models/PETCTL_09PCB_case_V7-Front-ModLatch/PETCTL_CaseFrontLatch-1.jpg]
Front_view_1

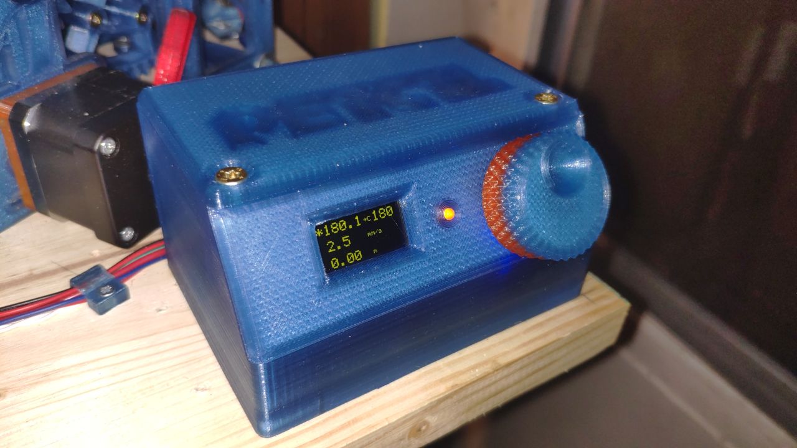
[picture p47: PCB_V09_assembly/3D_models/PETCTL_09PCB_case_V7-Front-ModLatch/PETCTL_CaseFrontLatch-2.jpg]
Front_view_2

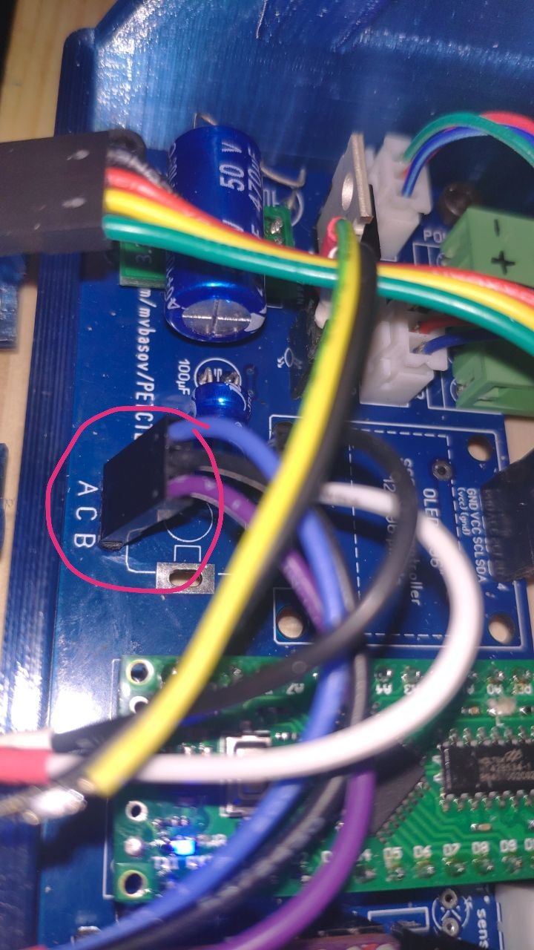
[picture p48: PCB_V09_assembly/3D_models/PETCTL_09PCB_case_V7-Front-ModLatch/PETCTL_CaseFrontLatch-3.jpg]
Front_view_3


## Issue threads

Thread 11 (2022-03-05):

PCB todo

mvbasov, 2022-03-05:
1. маску у конденсатора между выводами энкодера добавить.
2. маску на перемычках питания OLED убрать.
3. маску вокруг анода HL2 добавить. Критично. Диаметр отверстия маленький - при заливе чистить очень тяжело. Сильно "капилярит".
4. проверить корпус ключа нагревателя. Для IRFZ44N маловат.
5. ключ, преобразователь питания, большой конденсатор - очень тесно.
6. Какой то из выводов пищалки сделать двойным. У меня шаг 5 мм.
7. Надписи под драйвером ШД и разъёмом ШД кверху ногами :)
8. Около разъёмов эндстопов сделать надписи G-V-S.
9. На плате нарисовать табличку, если места хватит, как ставить перемычки на какой микрошаг.
10. USB разъём должен быть на стороне противоположной остальным разъёмам или лучше на узкой стороне.
11. проверить разводку вокруг разъёма термистора.
12. на схеме сделать левый верхний вывод энкодера землёй что бы соответствовало плате.

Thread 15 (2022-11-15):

PETCTL

Oleg9965, 2022-11-15:
Здравствуйте Михаил!
Повторил вашу конструкцию PETCTL.
Хотелось бы узнать, возможно ли немного изменить прошивку?
Добавить возможность реверса двигателя.
Что бы при вращении энкодера влево после 0, менялось направление вращения и
отображалось значение скорости со знаком -.

mvbasov, 2023-09-15:
Думаю, что это не сложно. Но делать не буду. Т.к. у меня нет в этом необходимости. Этот проект не имеет целью сделать что то удобное и универсальное для всех. Делается только для себя. Просто выложил свои наработки.

mvbasov, 2023-09-15:
См. предыдущий комментарий.

mvbasov, 2023-09-15:
Думаю, что это не сложно. Но делать не буду. Т.к. у меня нет в этом необходимости. Этот проект не имеет целью сделать что то удобное и универсальное для всех. Делается только для себя. Просто выложил свои наработки.

mvbasov, 2023-09-15:
См. предыдущей комментарий.

Closed 2023-09-15.

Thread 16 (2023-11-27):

Небольшие вопросы по работе petctl.

LexResident, 2023-11-27:
Благодарю за замечательный проект с исходным кодом. Собрал, всё устраивает.
Возник вопрос, в схеме и на плате есть hl2 и ext1, висят на d10, которых я в прошивке не нашёл, там должен быть вентилятор, но он не задействован?
И ещё, заливал прошивку пид регулятора, на процедуре calculate идёт постоянный перегрев. Посмотрел осциллографом на выводе нагревателя 30% заполнения шим. Я так понимаю этого много для моего нагревателя, и он продолжает жарить, как это можно вылечить, чтобы пиды посчитались верно. Удалось 1 раз завершить расчёт только нацепив на нагревателя радиатор, но тогда пиды не соответствуют стабильности системы. Какую строчку необходимо поправить чтобы уменьшить шим во время расчёта?

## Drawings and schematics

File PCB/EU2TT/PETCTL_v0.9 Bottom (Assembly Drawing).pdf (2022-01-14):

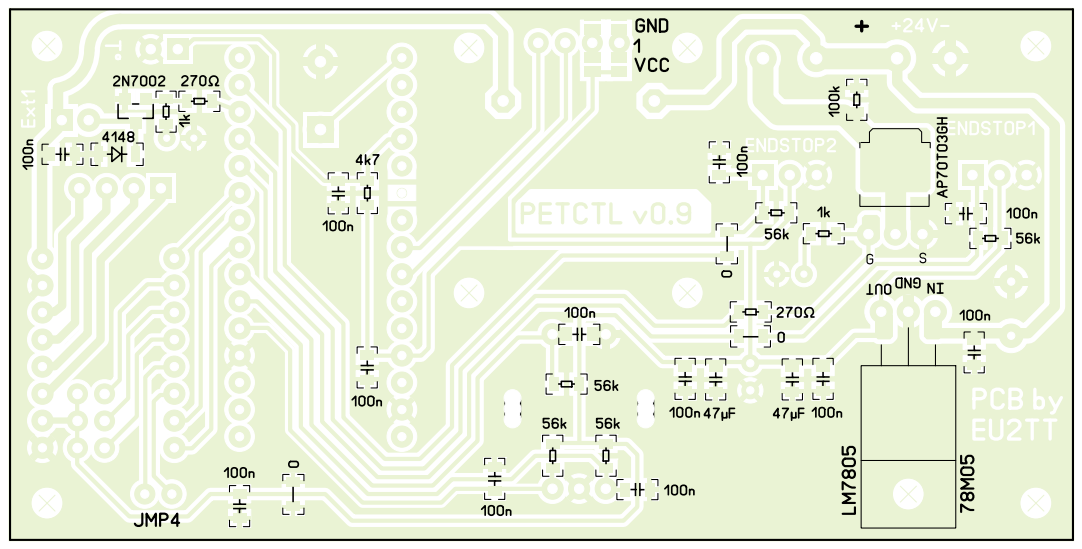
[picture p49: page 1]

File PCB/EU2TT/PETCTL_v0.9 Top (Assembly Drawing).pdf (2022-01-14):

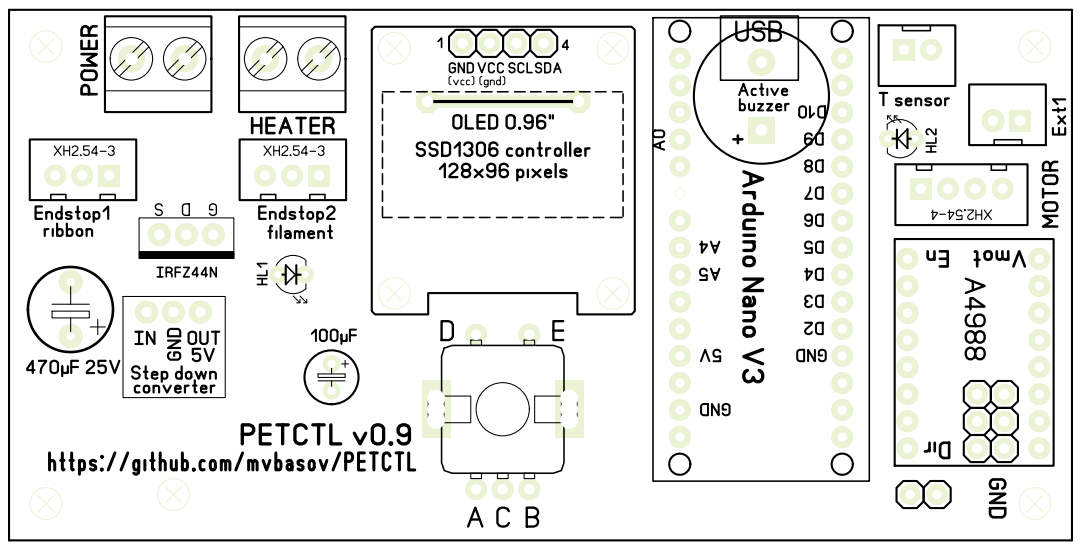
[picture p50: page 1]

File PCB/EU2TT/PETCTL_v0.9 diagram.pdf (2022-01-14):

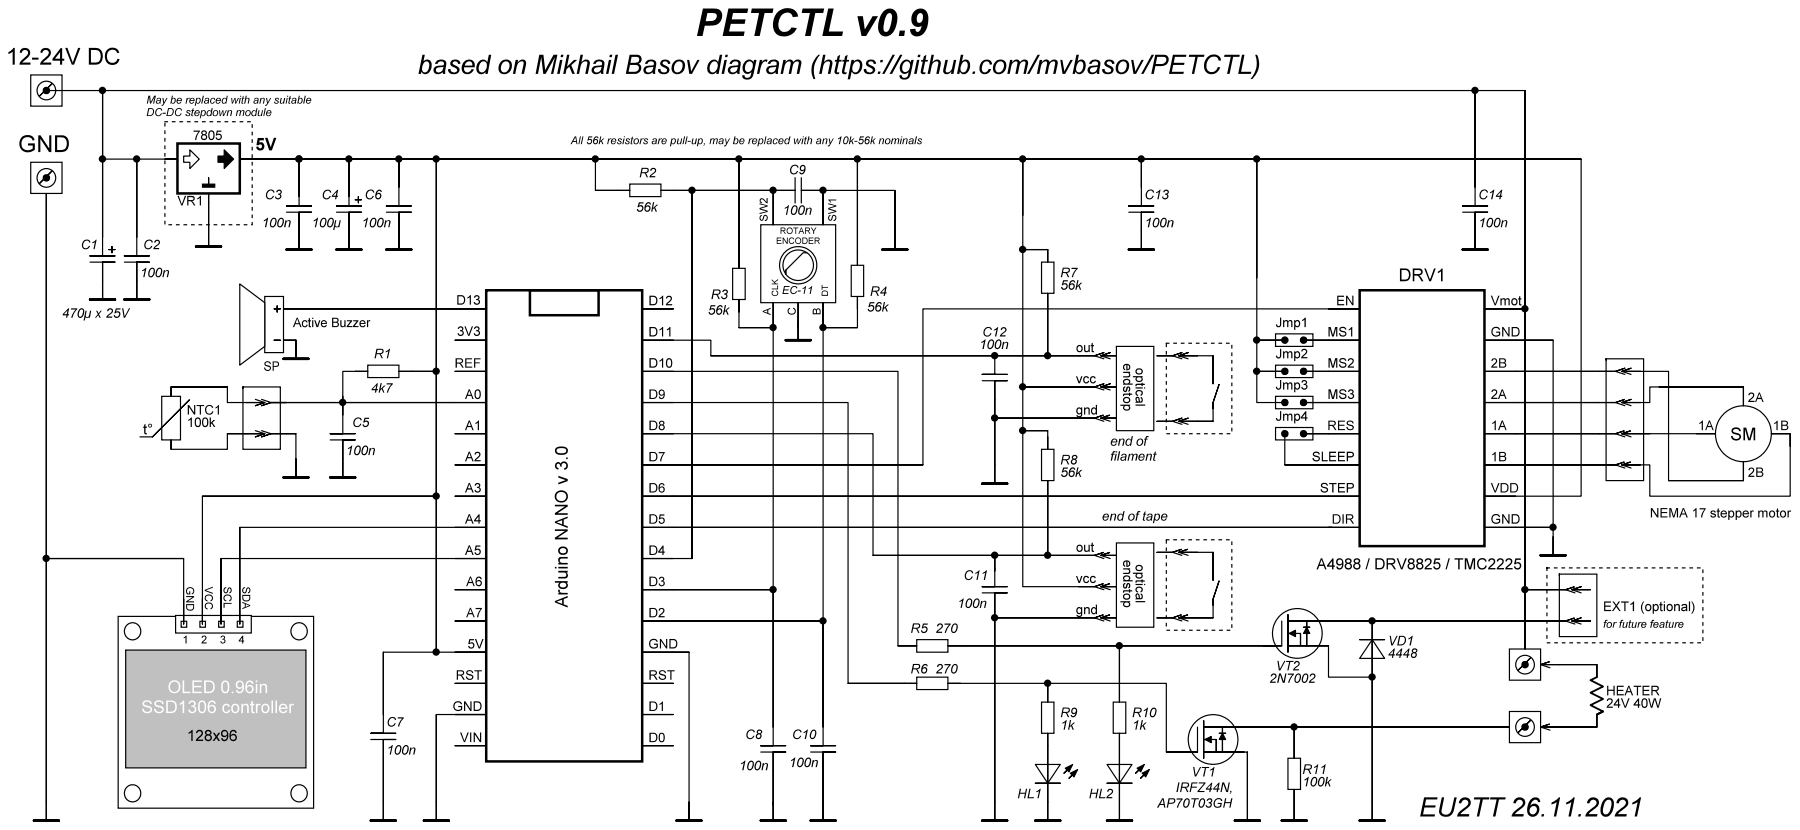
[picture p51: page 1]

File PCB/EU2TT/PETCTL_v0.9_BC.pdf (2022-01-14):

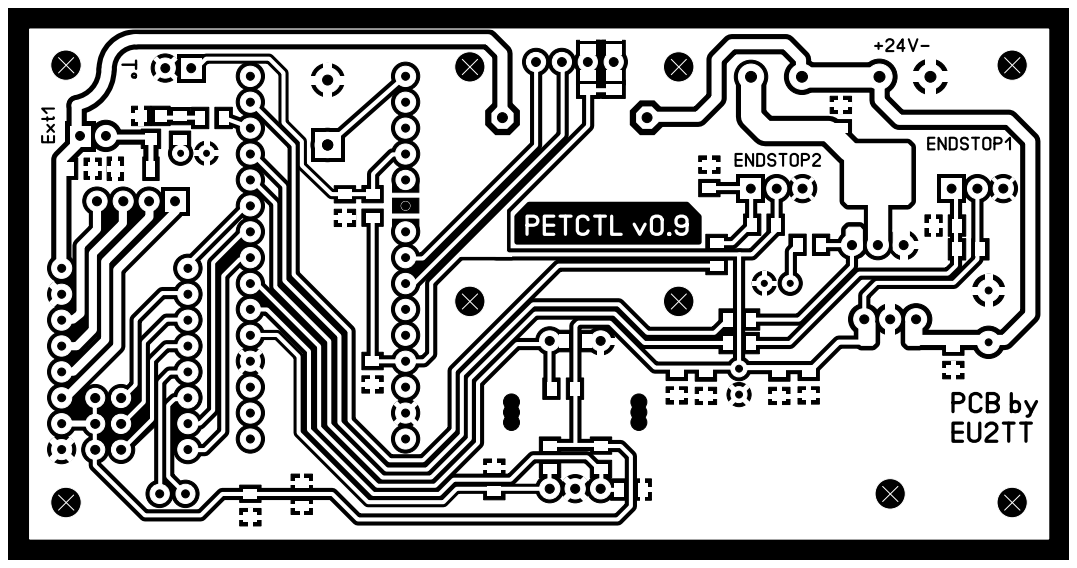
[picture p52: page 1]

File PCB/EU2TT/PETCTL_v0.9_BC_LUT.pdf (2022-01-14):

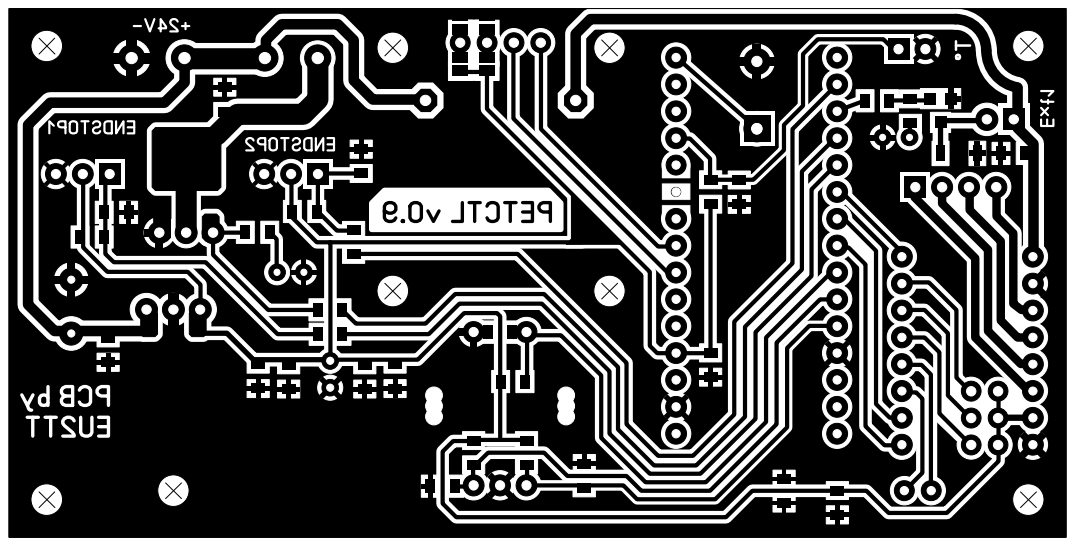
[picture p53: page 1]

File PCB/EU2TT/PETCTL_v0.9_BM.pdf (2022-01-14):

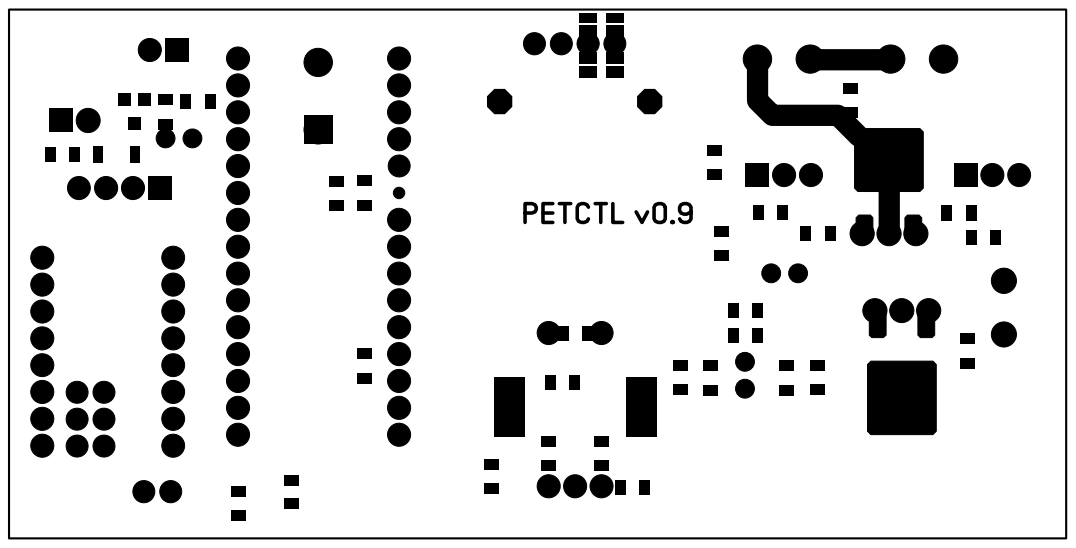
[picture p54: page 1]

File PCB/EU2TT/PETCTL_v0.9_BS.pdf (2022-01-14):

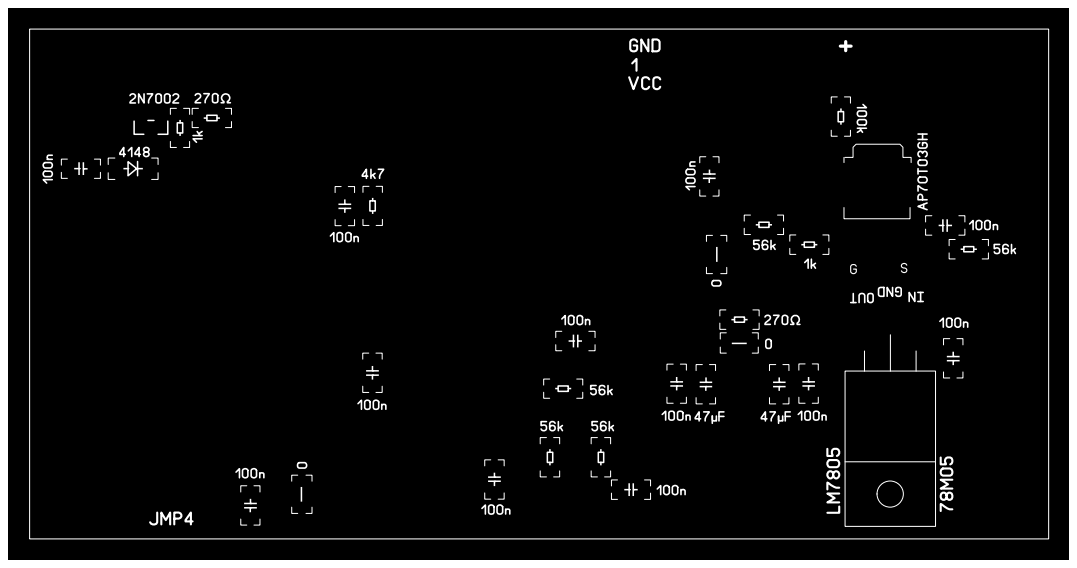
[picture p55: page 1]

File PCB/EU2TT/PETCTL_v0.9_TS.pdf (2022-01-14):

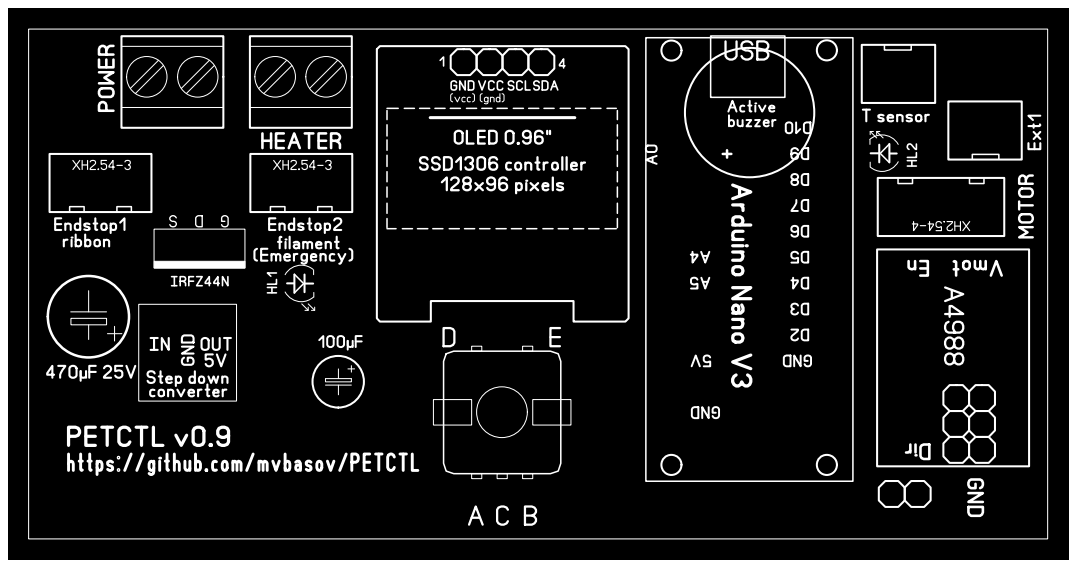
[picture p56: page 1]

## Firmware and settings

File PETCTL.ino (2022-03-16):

#include "PETCTL_cfg.h"
#define SPEED_MAX 10

#define DRIVER_STEP_TIME 6  // меняем задержку на 6 мкс
#include "GyverStepper.h"
GStepper<STEPPER2WIRE> stepper(200 * CFG_STEP_DIV, CFG_STEP_STEP_PIN, CFG_STEP_DIR_PIN, CFG_STEP_EN_PIN);

#include "GyverTimers.h"

#include "GyverOLED.h"
GyverOLED<SSD1306_128x64, OLED_NO_BUFFER> oled;

#define CLK CFG_ENC_CLK
#define DT CFG_ENC_DT
#define SW CFG_ENC_SW
#include "GyverEncoder.h"
Encoder enc1(CLK, DT, SW);
int value = 0;

// Termistor definition
float prevTemp, curTemp = 0;
float targetTemp = CFG_TEMP_INIT;

float finalLength = 0;

#include "GyverPID.h"
GyverPID regulator(CFG_PID_P, CFG_PID_I, CFG_PID_D, 200);

boolean Heat = false;

#define GEAR_RATIO ((float)CFG_RED_G1 * (float)CFG_RED_G2 * (float)CFG_RED_G3)
/*
Bobin round length
 74 * Pi = 232.478
 232.478 mm - bobin round length
*/
#define BOBIN_ROUND_LENGTH ((float)3.1415926 * (float)CFG_BOBIN_DIAM)
const float REDCONST = BOBIN_ROUND_LENGTH /(360 * GEAR_RATIO * 1000);
boolean runMotor=false;
long SpeedX10 = (float)CFG_SPEED_INIT * 10;

/* Interactive statuses */
#define CHANGE_NO 0
#define CHANGE_TEMPERATURE 1
#define CHANGE_SPEED 2
int whatToChange = CHANGE_NO;
unsigned long interactive = millis();

/* Emergency stop reasons */
#define OVERHEAT 1
#define THERMISTOR_ERROR 2

void encRotationToValue (long* value, int inc = 1, long minValue = 0, long maxValue = 0);

void setup() {

#if defined(SERIAL_DEBUG_TEMP) || defined(SERIAL_DEBUG_STEPPER) || defined(SERIAL_DEBUG_TEMP_PID)
  Serial.begin(9600);
#endif //SERIAL_DEBUG_TEMP || SERIAL_DEBUG_STEPPER
#if defined(SERIAL_DEBUG_STEPPER)
  Serial.print("Gear ratio: ");
  Serial.println(GEAR_RATIO);
  Serial.println("[deg/s],\t[step/s],\t[deg],\t[mm/s],\t[deg/s],\t[deg]");
#endif //SERIAL_DEBUG_STEPPER

#if defined(__LGT8F__)
  analogReadResolution(10);
#endif

  pinMode(CFG_ENDSTOP_PIN, INPUT_PULLUP);
  pinMode(CFG_EMENDSTOP_PIN, INPUT_PULLUP);
  pinMode(CFG_SOUND_PIN, OUTPUT);
  
  stepper.setRunMode(KEEP_SPEED);   // режим поддержания скорости
#if defined(CFG_STEP_INVERT)
  stepper.reverse(true);            // reverse direction
#endif //CFG_STEP_INVERT
  stepper.autoPower(true);
  stepper.setAcceleration(300);
  stepper.setSpeedDeg(mmStoDeg((float)SPEED_MAX));
  Timer2.setPeriod(stepper.getMinPeriod() / 2);
  stepper.brake();
  Timer2.enableISR();
  stepper.reset();                  // остановка и сброс позиции в 0
 
  oled.init();              // инициализация
  // ускорим вывод, ВЫЗЫВАТЬ ПОСЛЕ oled.init()!!!
  Wire.setClock(400000L);   // макс. 800'000
  oled.clear();
  
 //заставка
#if defined(CFG_SOUND_START)
  beepE();
#endif
  oled.setScale(3);
  oled.setCursor(13, 2);
  oled.println("PETCTL");
  oled.setScale(1);
  oled.setCursor(20, 7);
  oled.print("mvb   V 0.11");
  delay(3000);
 
  oled.clear();
  oled.setScale(1);
  oled.setCursorXY(74,5);
  oled.println("*C");
  oled.setCursorXY(75,5+5+16);
  oled.println("mm/s");
  oled.setCursorXY(78,5+5+5+5+32);
  oled.println("m");

  enc1.setType(CFG_ENC_TYPE);
  enc1.setPinMode(LOW_PULL);

  regulator.setpoint = targetTemp;
  printSpeed(SpeedX10);
  printTargetTemp(targetTemp);
  printMilage(0.0);
}

// обработчик
ISR(TIMER2_A) {
  enc1.tick();
  stepper.tick(); // тикаем тут
}

void yield() {
  // костыль, на всякий случай.
  stepper.tick();
}

void loop() {
    enc1.tick();
    stepper.tick();

    long newTargetTemp = targetTemp;
    long newSpeedX10 = SpeedX10;
    float rest;

    if (enc1.isDouble()) {
      whatToChange = CHANGE_SPEED;
      interactiveSet();
      printTargetTemp(targetTemp); // to clear selection
      printSpeed(SpeedX10);
    }
    if (enc1.isSingle()) {
      whatToChange = CHANGE_TEMPERATURE;
      interactiveSet();
      printSpeed(SpeedX10); // to clear selection
      printTargetTemp(targetTemp);
    }
    if (!isInteractive()) {
      whatToChange = CHANGE_NO;
      printSpeed(SpeedX10); // to clear selection
      printTargetTemp(targetTemp);
    }

    if( whatToChange == CHANGE_TEMPERATURE) {
      encRotationToValue(&newTargetTemp, 1, CFG_TEMP_MIN, CFG_TEMP_MAX - 10);
      if (enc1.isHolded()){
        Heat = ! Heat;
        printHeaterStatus(Heat);
      }

      if (newTargetTemp != targetTemp) {
        targetTemp = newTargetTemp;
        regulator.setpoint = newTargetTemp;
        printTargetTemp(newTargetTemp);
      }
    } else if (whatToChange == CHANGE_SPEED) {
      encRotationToValue(&newSpeedX10, 1, 0, SPEED_MAX * 10);
      if (enc1.isHolded()) {
        runMotor = ! runMotor;
        if (runMotor) {
          motorCTL(newSpeedX10);
        } else {
          motorCTL(-1);
          runMotor = false;
        }
        interactiveSet();
      }
      if (newSpeedX10 != SpeedX10) {
        SpeedX10 = newSpeedX10;
        if (runMotor) motorCTL(newSpeedX10);        // в градусах/сек
        printSpeed(newSpeedX10);
      }
    }
    if (runMotor) {
      printMilage(stepper.getCurrentDeg());
    }

    curTemp = getTemp();
    stepper.tick();
    if (curTemp > CFG_TEMP_MAX - 10) emStop(OVERHEAT);
    if (curTemp < -10) emStop(THERMISTOR_ERROR);
    regulator.input = curTemp;
    if (curTemp != prevTemp) {
      prevTemp = curTemp;
      printCurrentTemp(curTemp);
    }
    if (Heat) {
      int pidOut = (int) constrain(regulator.getResultTimer(), 0, 255);
      analogWrite(CFG_HEATER_PIN, pidOut);
      debugTemp(curTemp, pidOut);
    } else {
      analogWrite(CFG_HEATER_PIN, 0);
      debugTemp(curTemp, 0);
    }

    oled.setCursorXY(90, 47);
    if(!digitalRead(CFG_ENDSTOP_PIN)) {
      if(!runMotor) {
        oled.setScale(2);
        oled.println("  *");
      } else {
        if (finalLength > 0){
          rest = finalLength - getMilage();
          if (rest >= 0) {
            oled.setScale(1);
            oled.setCursorXY(90, 55);
            oled.println(rest*100,1); // rest in cm
            oled.setScale(2);
          } else {
            runMotor = false;
            motorCTL(0);
            Heat = false;
            printHeaterStatus(Heat);
            finalLength = 0;
            beepI();
          }
        } else {
          finalLength = getMilage() + CFG_PULL_EXTRA_LENGTH;
        }
      }
    } else {
      oled.setScale(2);
      oled.println("   ");
      finalLength = 0;
    }
    
    oled.setCursorXY(112, 24);
    if(!digitalRead(CFG_EMENDSTOP_PIN)) {
      if(!runMotor) {
        oled.setScale(2);
        oled.println("X");
      } else {
        runMotor = false;
        motorCTL(-1);
        Heat = false;
        printHeaterStatus(Heat);
        beepI();
        beepI();
       }
    } else {
      oled.setScale(2);
      oled.println(" ");
    } 
}

void debugTemp(float temp, int out) {
#if defined(SERIAL_DEBUG_TEMP)
    static long debug_time;
    if (debug_time < millis() ) {
      debug_time = millis() + 200;
      Serial.print(temp);
#if defined(SERIAL_DEBUG_TEMP_PID)
      Serial.print(' ');
      Serial.print(out);
#endif // end SERIAL_DEBUG_TEMP_PID
      Serial.println(' ');
    }
#endif //end SERIAL_DEBUG_TEMP
}

long mmStoDeg(float mmS) {
  return mmS / (REDCONST * 1000);
}

void beepE() {
  digitalWrite(CFG_SOUND_PIN, 1);
  delay(50);
  digitalWrite(CFG_SOUND_PIN, 0);
  delay(50);
}

void beepI() {
  beepE();
  beepE();
}
void beepT() {
  digitalWrite(CFG_SOUND_PIN, 1);
  delay(600);
  digitalWrite(CFG_SOUND_PIN, 0);
  delay(200);
}

void beepO() {
  beepT();
  beepT();
  beepT();
}

void emStop(int reason) {
  runMotor = false;
  motorCTL(-1);
  stepper.disable();
  Heat = false;
  analogWrite(CFG_HEATER_PIN, 0);
  oled.clear();
  oled.setScale(3);
  oled.setCursorXY(0,2);
  oled.println("*HALT!*");
  oled.setScale(2);
  oled.setCursorXY(3,40);
  switch (reason) {
    case OVERHEAT:
      oled.println("Overheat");
      break;
    case THERMISTOR_ERROR:
      oled.println("Thermistor");
      break;
  }
  for(;;){
    beepO();
    delay(60000);
  }
}
 
float getMilage() {
  return stepper.getCurrentDeg() * REDCONST;
}

void motorCTL(long setSpeedX10) {
#if defined(SERIAL_DEBUG_STEPPER)
  Serial.print(stepper.getSpeedDeg());
  Serial.print(",\t");
  Serial.print(stepper.getSpeed());
  Serial.print(",\t");
  Serial.print(stepper.getCurrent());
  Serial.print(",\t");
#endif // SERIAL_DEBUG_STEPPER
  oled.setScale(2);
  oled.setCursorXY(0, 23);

  if (setSpeedX10 > 0) {
    stepper.setSpeedDeg(mmStoDeg((float)setSpeedX10/10), SMOOTH);        // [degree/sec]
    oled.println("*");
  } else if (setSpeedX10 == 0) {
    stepper.stop();
    oled.println(".");
  } else {
    stepper.brake();    
    oled.println(".");
  }
  
#if defined(SERIAL_DEBUG_STEPPER)
  Serial.print((float)setSpeedX10/10);
  Serial.print(",\t");
  Serial.print(stepper.getSpeedDeg());
  Serial.print(",\t");
  Serial.print(stepper.getCurrent());
  Serial.println(" ");
#endif // SERIAL_DEBUG_STEPPER

}

void printHeaterStatus(boolean status) {
  oled.setCursorXY(0, 0);
  if(status) 
    oled.println("*");
  else
    oled.println(".");
}

void encRotationToValue (long* value, int inc = 1, long minValue = 0, long maxValue = 0) {
      if (enc1.isRight()) { *value += inc; interactiveSet(); }     // если был поворот направо, увеличиваем на 1
      if (enc1.isFastR()) { *value += inc * 5; interactiveSet(); }    // если был быстрый поворот направо, увеличиваем на 10
      if (enc1.isLeft())  { *value -= inc; interactiveSet(); }     // если был поворот налево, уменьшаем на 1
      if (enc1.isFastL()) { *value -= inc * 5; interactiveSet(); }    // если был быстрый поворот налево, уменьшаем на на 10
      //if (minValue > 0 && *value < minValue) *value = minValue;
      if (*value < minValue) *value = minValue;
      //if (maxValue > 0 && *value > maxValue) *value = maxValue;
      if (*value > maxValue) *value = maxValue;
}

void printTargetTemp(float t){
      oled.setScale(2);      
      if(whatToChange == CHANGE_TEMPERATURE)  oled.invertText(true);
      oled.setCursorXY(88, 0);
      oled.println((int)t, 1);  
      oled.invertText(false);
}

void printCurrentTemp(float t) {
      oled.setScale(2);      
      oled.setCursorXY(12, 0);
      oled.print(t, 1);   
      if (t < 99.9) oled.print(" "); //clean screen garbage
      if (t < 9.9) oled.print(" ");
}

void printSpeed(long s){
      // s -speed in mm/s * 10
      // // pint in mm/s
      oled.setScale(2);      
      oled.setCursorXY(12, 23);
      if(whatToChange == CHANGE_SPEED)  oled.invertText(true);
      oled.print((float)s/10, 1);
      if (s<100) oled.print(" "); //fix display garbage 
      oled.invertText(false);
}

void printMilage(float m){
      // m - current stepper position in degree
      // output to display in meters
      oled.setScale(2);
      oled.setCursorXY(12, 47);
      oled.println(m * REDCONST);  
}

void interactiveSet() {
  interactive = millis() + 15000;
}

boolean isInteractive() {
  return millis() < interactive;
}

float getTemp() {
  uint8_t i;
  float average;

  average = analogRead(CFG_TERM_PIN);
  // convert the value to resistance
  average = 1023 / average - 1;
  average = CFG_TERM_SERIAL_R / average;

  float steinhart;
  steinhart = average / CFG_TERM_VALUE;     // (R/Ro)
  steinhart = log(steinhart);                  // ln(R/Ro)
  steinhart /= CFG_TERM_B_COEFF;                   // 1/B * ln(R/Ro)
  steinhart += 1.0 / (CFG_TERM_VALUE_TEMP + 273.15); // + (1/To)
  steinhart = 1.0 / steinhart;                 // Invert
  steinhart -= 273.15;                         // convert absolute temp to C

  return simpleKalman(steinhart);
}

// Простой “Калман” 
// https://alexgyver.ru/lessons/filters/
float _err_measure = 0.8;  // примерный шум измерений
float _q = 0.02;   // скорость изменения значений 0.001-1, варьировать самому

float simpleKalman(float newVal) {
  float _kalman_gain, _current_estimate;
  static float _err_estimate = _err_measure;
  static float _last_estimate;
  _kalman_gain = (float)_err_estimate / (_err_estimate + _err_measure);
  _current_estimate = _last_estimate + (float)_kalman_gain * (newVal - _last_estimate);
  _err_estimate =  (1.0 - _kalman_gain) * _err_estimate + fabs(_last_estimate - _current_estimate) * _q;
  _last_estimate = _current_estimate;
  return _current_estimate;
}

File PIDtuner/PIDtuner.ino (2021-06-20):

#include "PETCTL_cfg.h"

#include "PIDtuner.h"
PIDtuner tuner;

#include "GyverOLED.h"
GyverOLED<SSD1306_128x64, OLED_NO_BUFFER> oled;

#define RUNTIME uint32_t(1200000) 
uint32_t startTime; 

void setup() {
  pinMode(CFG_SOUND_PIN, OUTPUT);
  
  oled.init();              // инициализация
  // ускорим вывод, ВЫЗЫВАТЬ ПОСЛЕ oled.init()!!!
  Wire.setClock(400000L);   // макс. 800'000

#if defined(CFG_SOUND_START)
  beepE();
#endif
  oled.clear();
  oled.setScale(3);
  oled.setCursor(10, 1);
  oled.println("PETCTL");
  oled.setCursor(30, 4);
  oled.println("PID");
  oled.setScale(1);
  oled.setCursor(20, 7);
  oled.print("mvb    V 0.1");
  delay(3000);
  oled.clear();
  
  static long debug_time = 0;
  Serial.begin(9600);
  Serial.print("Cool down to ");
  Serial.print(CFG_TEMP_INIT - 10);
  Serial.println("C");
  analogWrite(CFG_HEATER_PIN, 0);
  getTemp();
  getTemp();
  //printPID(1000, 1111.11, 2222.22, 3333.33); //for test screen garbage cleaning
  while (getTemp() > CFG_TEMP_INIT - 10.0) {
    if (debug_time < millis() ) {
      debug_time = millis() + 2000;
      Serial.println(getTemp());
      printTemp(getTemp());
      printStatus("Cool Down");
    }
  }
  Serial.print("Heat up to "); 
  Serial.print(CFG_TEMP_INIT);
  Serial.println("C");
  analogWrite(CFG_HEATER_PIN, 128);
  while (getTemp() < CFG_TEMP_INIT + 0.0) {
    if (debug_time < millis() ) {
      debug_time = millis() + 2000;
      Serial.println(getTemp());
      printTemp(getTemp());
      printStatus("Heat Up  ");
    }
  }
  analogWrite(CFG_HEATER_PIN, 0);
  // направление, сигнал, ступенька, период стабилизации, точность стабилизации, продолж. импульса, период итерации  
  tuner.setParameters(NORMAL, 80, 15, 5000, 0.08, 10000, 200);
  startTime = millis();
  Serial.println(startTime);
  beepE();
}
void loop() {
  static float pidP;
  static float pidI;
  static float pidD;
  static int accuracy=0;
  static unsigned long when=millis(); 
  static float curTemp; 

  curTemp = getTemp();
  if (curTemp > 230) {
    analogWrite(CFG_HEATER_PIN, 0);
    Serial.print("*** OVERHEAT 230C ***: ");
    Serial.println(curTemp);
    printTemp(curTemp);
    printStatus("OverHeat!");
    while(1){
        printTemp(getTemp());
    }
  }
  
  tuner.setInput(curTemp);
  tuner.compute();
  analogWrite(CFG_HEATER_PIN, tuner.getOutput());

  if (when < millis()) {
    when = millis() + 10000;
    printTemp(curTemp);
    if(accuracy <= tuner.getAccuracy()){
      accuracy = tuner.getAccuracy();
      pidP=tuner.getPID_p();
      pidI=tuner.getPID_i();
      pidD=tuner.getPID_d();
      printPID(accuracy, pidP, pidI, pidD);
      printStatus("Calculate");
    }
  }

  // выводит в порт текстовые отладочные данные, включая коэффициенты
  tuner.debugText();

  // выводит в порт данные для построения графиков, без коэффициентов
  //tuner.debugPlot();
  long rTime = millis() - startTime;
  printTimer(RUNTIME - rTime);
  if(rTime >= RUNTIME){
    analogWrite(CFG_HEATER_PIN, 0);
    Serial.println(millis()- startTime );
    Serial.println(RUNTIME );
    Serial.println("*** Final result: ***");
    Serial.print("A:");
    Serial.print(accuracy); 
    Serial.print(", P:");
    Serial.print(pidP); 
    Serial.print(", I:");
    Serial.print(pidI); 
    Serial.print(", D:");
    Serial.print(pidD);
    Serial.println(" ");       
    printPID(accuracy, pidP, pidI, pidD);
    printStatus("Done!    ");
    beepI();

    while(1){
      printTemp(getTemp());
    }

  }

}

void beepE() {
  digitalWrite(CFG_SOUND_PIN, 1);
  delay(50);
  digitalWrite(CFG_SOUND_PIN, 0);
  delay(50);
}

void beepI() {
  beepE();
  beepE();
}

void printTemp(float temp){
      oled.setScale(1);      
      oled.setCursor(85, 1);
      oled.print("       ");
      oled.setCursor(90, 1);
      oled.print("T: ");
      oled.println((int)temp, 1);  
}

void printPID(int A, float P, float I, float D){
      static char tbuf[8];
      oled.setScale(1);      
      oled.setCursor(1, 1);
      oled.print("          ");
      oled.setCursor(1, 1);
      oled.print("A: ");
      oled.println(A);
      oled.setCursor(1, 3);
      oled.print("          ");
      oled.setCursor(1, 3);
      oled.print("P: ");
      oled.print(P,2);  
      oled.setCursor(1, 5);
      oled.print("          ");
      oled.setCursor(1, 5);
      oled.print("I: ");
      oled.print(I,2);
      oled.setCursor(1, 7);  
      oled.print("          ");
      oled.setCursor(1, 7);  
      oled.print("D: ");
      oled.print(D,2);  
}

void printStatus(String s){
      oled.setScale(1);      
      oled.setCursor(65, 7);
      oled.println(s);  
  
}

void printTimer(long msec){
      static char tbuf[6];
      int sec = msec / 1000;
      sprintf_P(tbuf,PSTR("%02d:%02d"), sec / 60, sec % 60);
      oled.setScale(1);      
      oled.setCursor(85, 5);
      oled.print(tbuf);  
}

float getTemp() {
  uint8_t i;
  float average;

  average = analogRead(CFG_TERM_PIN);
  // convert the value to resistance
  average = 1023 / average - 1;
  average = CFG_TERM_SERIAL_R / average;
  //Serial.print("Thermistor resistance ");
  //Serial.println(average);

  float steinhart;
  steinhart = average / CFG_TERM_VALUE;     // (R/Ro)
  steinhart = log(steinhart);                  // ln(R/Ro)
  steinhart /= CFG_TERM_B_COEFF;                   // 1/B * ln(R/Ro)
  steinhart += 1.0 / (CFG_TERM_VALUE_TEMP + 273.15); // + (1/To)
  steinhart = 1.0 / steinhart;                 // Invert
  steinhart -= 273.15;                         // convert absolute temp to C

  return simpleKalman(steinhart);
}

// Простой “Калман”
// https://alexgyver.ru/lessons/filters/
float _err_measure = 0.8;  // примерный шум измерений
float _q = 0.02;   // скорость изменения значений 0.001-1, варьировать самому

float simpleKalman(float newVal) {
  float _kalman_gain, _current_estimate;
  static float _err_estimate = _err_measure;
  static float _last_estimate;
  _kalman_gain = (float)_err_estimate / (_err_estimate + _err_measure);
  _current_estimate = _last_estimate + (float)_kalman_gain * (newVal - _last_estimate);
  _err_estimate =  (1.0 - _kalman_gain) * _err_estimate + fabs(_last_estimate - _current_estimate) * _q;
  _last_estimate = _current_estimate;
  return _current_estimate;
}

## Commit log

2021-01-10 Termometer operate and display temperature
2021-01-10 Display temperature only if changed
2021-01-11 Use Proportional on Measurement PID mode
2021-01-12 Set Temperature by encoder
    And more realistic PID coefecients
2021-01-12 Use PID V2 library
2021-01-16 Start rewrite to Gyver libs
    Doble click encoder to start motor at 530 degree per second...
2021-01-18 Add temperature controll
2021-01-18 Use old experimentaly found PID parameters
2021-01-18 Add PID library to git
2021-01-19 It can be named ALPHA version :) 12 m of filament produced.
2021-01-20 Fix set motor speed bug
    [PETCTL.ino]
2021-01-22 Use Kalman (simple) filter for temperature.
2021-01-23 Gear ratio accurate calculation
2021-04-14 Prepare to next release
    - Add EndStop processing
    - Chenge temperature measurement algoritm
2021-04-15 Fix wrong macros substitution
    [PETCTL.ino]
2021-04-16 Add 3D models
    [CableClip_V1.FCStd, CableClip_V1.stl, EndStopFlag_V2.stl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]
2021-04-16 Update schematic
2021-04-18 Update GyverOLED library to fix intro screen
    [GyverOLED.h]
2021-04-19 Fix reduction ratio for PETPull-2
    [PETCTL_cfg.h]
2021-05-01 Fix 1/8 microstep operation
    [PETCTL.ino, PETCTL_cfg.h]
2021-05-12 Add limits to allowed temperature settings
2021-05-12 Unify motor control algorithm
2021-05-12 Overheat an thermistor break protection
    [PETCTL.ino, PETCTL_cfg.h]
2021-05-15 Add sound (active buzzer) support
    [PETCTL.ino, PETCTL_cfg.h]
2021-05-15 Add sound to error status
    [PETCTL.ino]
2021-05-19 Readme.md for EU2TT PCB.
2021-05-19 Add EU2TT circuit diagram to title page
2021-05-19 Fix circuit diagram display on title page
2021-05-19 BOM initial edition
2021-05-19 Reference to BOM
2021-05-19 Move BOM content from README page
2021-05-19 Motor EN
2021-05-29 Add encoder type to config
2021-05-29 Fix PETPull classic reductor definition
    [PETCTL_cfg.h]
2021-05-29 Debug for stepper speed
2021-05-29 Change stepper debug output format
2021-05-30 Add stepper position to debug
2021-06-06 Rewrite stepper code as tested on bugreport sketch
    [PETCTL.ino]
2021-06-16 Reorganize TEMP/PID debug
2021-06-16 Tune PID
2021-06-20 PID tuner operatable version
2021-06-20 Fix display garbage at speed diplay
    [PETCTL.ino]
2021-06-20 Fix screen garbage at temperature display
    [PETCTL.ino]
2021-06-20 Add README to PID tuner
2021-06-20 Upload PID tuner screen
2021-06-20 Add info about endstop
2021-06-28 Add Heated Block documentation
    [FilPullHB_v1c.FCStd]
2021-06-29 Add Fuzer documentation
    [FilPullNozzle_v2a.FCStd]
2021-06-29 Update heated block documentation
    [FilPullNozzle_v2a.FCStd]
2021-06-29 Update fuser documentation
    [FilPullNozzle_v2a.FCStd]
2021-06-29 Uhdate README.md for fuser
2021-06-29 Add images to fuser REDME.md
2021-09-10 Add files via upload
    Добавил оригинальный файл в Sprint Layout, "фотографию" платы, рисунки шелкографии на верхней стороне платы, монтажную схему нижней стороны и рисунок платы для изготовления по технологии ЛУТ. При печ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
2021-09-25 Add endstop case 3D models
    [OptoEndStopCase_v2.FCStd, OptoEndStopCase_v2.step, OptoEndStopCase_v2.stl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]
2021-09-25 Cleanup 3D models catalog
    [CableClip_V1.step, EndStopFlag_V2.stl, EndStopMount_V1.FCStd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]
2021-09-25 Add stepper invertion to config
2021-11-04 Add new Opto EndStop files
    [OptoEndStopCase_v4.FCStd, OptoEndStopCase_v4.stl, OptoEndStopCase_v5.FCStd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]
2021-11-06 Optical sensor info
2021-11-06 PCB link
2021-11-06 Add fuser link
2021-12-23 Add emergency endstop support
2022-01-05 Remove UTF BOM from GyverOLED.h
2022-01-10 Схема, рисунок и Gerber файлы платы v0.9
    Плата контроллера PETCTL v 0.9
    Основная идея проекта - возможность его повторения всеми желающими. Печатную плату можно сделать используя ЛУТ или заказать на любом из сервисов, к примеру JLCPCB. Архив с GERBER-файлами прилагается.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
2022-01-12 Revert "Delete PCB/EU2TT directory"
    This reverts commit 480e81d40a45458a04bbd7974fb805ef372d8335.
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2022-01-14 Схема, рисунок и Gerber файлы платы v0.9
2022-01-14 PCB README style little changed
2022-02-23 First variant of PCB v0.9 case
    [ETCTL_09PCB_case_V1.FCStd, ETCTL_09PCB_case_V1.stl, ETCTL_09PCB_case_V2.FCStd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]
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2022-02-23 Add PCB version status
2022-02-24 Default encoder type is TYPE2 now.
2022-02-24 Next variant of case for v0.9 PCB
    Without top-back cover, this time.
    [PETCTL_09PCB_case_V5.FCStd, PETCTL_09PCB_case_V5.stl, PETCTL_09PCB_case_V5_front.stl]
2022-02-25 Cleanup old case models
    [ETCTL_09PCB_case_V1.FCStd, ETCTL_09PCB_case_V1.stl, ETCTL_09PCB_case_V2.FCStd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]
2022-02-25 Usable version of case for PCB v0.9
    [PETCTL_09PCB_case_V6-Base.stl, PETCTL_09PCB_case_V6-Front.stl, PETCTL_09PCB_case_V6-TopBack.stl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]
2022-02-25 Add encoder knob and delete unused files
    [EncoderKnob-V2.stl, PETCTL_stand_L_V3.step, PETCTL_stand_L_V3.stl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]
2022-02-26 Add DC-DC to BOM
2022-02-26 Fix BOM page format
2022-03-05 Add LGT8F328P LQFP32 to BOM
2022-03-05 Draft of PCB assemble guide
2022-03-05 PCB to case assemble guide (draft)
    [PETCTL_09PCB_case_V6-Base.stl, PETCTL_09PCB_case_V6-Front.stl, PETCTL_09PCB_case_V6-TopBack.stl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]
2022-03-05 Fix assembly guide misstypes
2022-03-05 Format PCB assemble guide
2022-03-05 Fix link to PCB description in PCB assembly guide
2022-03-05 Add power supply information
2022-03-05 Add thermistor and heater info to BOM
2022-03-06 New case with project logo
    [PETCTL_09PCB_case_V6-Base.stl, PETCTL_09PCB_case_V6-Front.stl, PETCTL_09PCB_case_V6-TopBack.stl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]
2022-03-06 Add about USB cable access to front page.
2022-03-06 Add version staus to assembly guide
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2022-03-06 Add about ISP to assemble guide
2022-03-06 Move knob files to case 3D models directory
    [EncoderKnob-20mm-V2.stl]
2022-03-06 Create README.md for 3D case files
2022-03-06 Add strip cleaner 3D files
    [StripeCleaner(asZenipas).FCStd, StripeCleaner(asZenipas).stl]
2022-03-13 Add 15 mm shaft encoder knob 3D model
    [EncoderKnob-15mm-V3.stl]
2022-03-16 Fix multi MCU type support
    Thanx Andrey Kudryavcev for bug report
    [PETCTL.ino]
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2022-03-17 Add about LED cable to assemble guide.
2022-07-06 add Latch files
    [PETCTL_CaseFrontLatch.step, PETCTL_CaseFrontLatch.stl]
